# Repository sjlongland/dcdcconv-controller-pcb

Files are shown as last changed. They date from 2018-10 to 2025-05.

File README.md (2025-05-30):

[Find this project on codeberg](https://codeberg.org/sjlongland/dcdcconv-controller-pcb)

As a result of Github's decision to force AI-generated issues with no opt-out,
I am migrating personal projects of mine to Codeberg.  The project at Github
will be archived.

----

# DC-DC Converter Controller

This PCB (using KiCAD 5.0) implements the controller for a DC-DC converter.
It provides differential I²C for connection to a [voltage/current sensor
board](https://codeberg.org/sjlongland/dcdcconv-sensor-pcb) and LVDS outputs for
connection to a [driver
board](https://codeberg.org/sjlongland/dcdcconv-driver-pcb).

The brains of the operation is the Atmel ATTiny861 microcontroller, which
features a high-speed PLL for fast PWM outputs.  The
[firmware](https://codeberg.org/sjlongland/dcdcconv-firmware) polls up to two
sensor boards to make decisions on the PWM duty cycle used to control the
MOSFET driver board.  In theory, the firmware can be expanded to support other
sensor boards and the MOSFET driver board replaced to support other switch
types such as IGBTs for higher power converters.  Use of differential
signalling minimises interference on long cable runs.

The ATTiny861 communicates with a host controller via SPI, allowing it to
communicate with a wide array of host controllers.  This allows for higher-end
host MCUs and application processors that perhaps aren't as good on the PWM
front, to receive notification of when voltage or current levels change
outside given bounds, and thus provide advice on how to adjust the PWM level
to meet requirements.

The host controller can provide the UI functions and higher-level algorithms
such as [MPPT](https://en.wikipedia.org/wiki/Maximum_power_point_tracking)
allowing the ATTiny861 to actually look after the PWM and low-level control.

## Parts list

### To omit:

* U2: Do not fit: for switch controller below only
* C2: Do not fit: localised decoupling for U2.
* J2: Do not fit: GPIO outputs for U2.

### To fit:

* U1: Atmel ATTiny861A-SU
* U3: 74AHC244 tri-state buffer
* U4: NXP PCA9615 Differential I²C controller
* U5: TI SN65LVDS047D 4-channel LVDS driver
* C5: ≥100µF ≥10V 6.3mm SMD electrolytic capacitor (bulk power rail decoupling)
* C1, C3, C4, C6: 100nF ≥10V 0805 ceramic capacitor (localised power rail
  decoupling)
* (**FIT ONE ONLY**) C7, C8, C9, C10: ~100pF ≥20V ceramic capacitor 0805 (0V
  AC de-coupling to chassis.  Choose the one that best suits your mounting
  requirements.)
* R1, R2: 2k2 ohm resistors, 0805 size (I²C pull-ups)
* R3, R4, R5, R6, R7: (approx) 10k ohm resistors, 0805 size (GPIO pull-ups)
* R8, R10: (**NOT CONFIRMED**) 2k2 ohm resistors, 0805 size (differential I²C
  pull-ups)
* R12, R15: (**NOT CONFIRMED**) 2k2 ohm resistors, 0805 size (differential I²C
  pull-downs)
* R9, R11, R12, R14: Spaces for additional pull-up/down resistors on
  differential I²C.  Do not fit unless found to be required.
* R16, R17: (**NOT CONFIRMED**) 100 ohm 0805 (differential I²C termination)
* R22, R26, R30, R34, R24, R28, R32, R36: Spaces for pull-up resistors on
  LVDS.  Do not fit unless found to be required.
* R23, R27, R31, R35, R25, R29, R33, R37: Spaces for pull-down resistors on
  LVDS.  Do not fit unless found to be required.
* R18, R19, R20, R21: Spaces for termination resistors on LVDS.  Do not fit
  unless found to be required.
* J1: 2×7 right-angle 2.54mm header connector (host SPI interface)
* J3, J4: 6-pin 2.54mm "KK" connector (Differential I²C to sensor boards,
  two provided for wiring convenience wired in parallel, use both or
  either.)
* J5: 6-pin 2.54mm "KK" connector (LVDS PWM outputs for buck converter
  MOSFETs)
* J6: 6-pin 2.54mm "KK" connector (LVDS PWM outputs for boost converter
  MOSFETs)

# Switch controller

The board also supports an alternate MCU, the Atmel ATTiny24A, which can be
used in place of the ATTiny861 for simple switch control.  In this
configuration, the LVDS output is dispensed with in favour of a pair of
low-speed GPIOs (one PWMable) which can drive a small signal transistor for
MOSFET control or directly drive solid-state relays.

This latter design is intended for applications such as
[VSRs](https://en.wikipedia.org/wiki/Voltage-sensitive_relay) and power
distribution control using an interface compatible with the full controller.
The controller still supports talking to multiple sensor boards for power
measurement.

## Parts list

### To omit:
* C1, C4, C6: Do not fit: localised decoupling for U1, U3, U5.
* U1, U3, U5: Do not fit: for PWM DC-DC controller above.
* R22, R26, R30, R34, R24, R28, R32, R36, R23, R27, R31, R35, R25, R29, R33,
  R37, R18, R19, R20, R21: Do not fit: pull resistors for LVDS (not used)
* J5, J6: Do not fit: LVDS outputs for PWM controller

### To fit:
* U2: Atmel ATTiny24A-SSU
* U4: NXP PCA9615 Differential I²C controller
* C5: ≥100µF ≥10V 6.3mm SMD electrolytic capacitor (bulk power rail decoupling)
* C2, C3: 100nF ≥10V 0805 ceramic capacitor (localised power rail
  decoupling)
* (**FIT ONE ONLY**) C7, C8, C9, C10: ~100pF ≥20V ceramic capacitor 0805 (0V
  AC de-coupling to chassis.  Choose the one that best suits your mounting
  requirements.)
* R1, R2: 2k2 ohm resistors, 0805 size (I²C pull-ups)
* R3, R4, R5, R6, R7: (approx) 10k ohm resistors, 0805 size (GPIO pull-ups)
* R8, R10: (**NOT CONFIRMED**) 2k2 ohm resistors, 0805 size (differential I²C
  pull-ups)
* R12, R15: (**NOT CONFIRMED**) 2k2 ohm resistors, 0805 size (differential I²C
  pull-downs)
* R9, R11, R12, R14: Spaces for additional pull-up/down resistors on
  differential I²C.  Do not fit unless found to be required.
* R16, R17: (**NOT CONFIRMED**) 100 ohm 0805 (differential I²C termination)
* J1: 2×7 right-angle 2.54mm header connector (host SPI interface)
* J2: 4-pin 2.54mm "KK" connector (GPIO outputs for MOSFET/SSR switch control)
* J3, J4: 6-pin 2.54mm "KK" connector (Differential I²C to sensor boards,
  two provided for wiring convenience wired in parallel, use both or
  either.)

# Host interface

The host interface is via the 14-pin connector at the bottom of the board.
This connector features the following signals:

* Even pins: 0V reference voltage
* Pin 1: 5V power rail
* Pin 3: SPI interface `MOSI` data input
* Pin 5: SPI interface `MISO` data output
* Pin 7: SPI interface `SCK` serial clock
* Pin 9: SPI interface `nCS` Chip select
* Pin 11: SPI interface `nINT` Host interrupt
* Pin 13: `nRESET` Device reset and AVR ICSP.
* Pin 15: `GPIO1` Arbitrary GPIO for application use
* Pin 17: `GPIO0` Arbitrary GPIO for application use

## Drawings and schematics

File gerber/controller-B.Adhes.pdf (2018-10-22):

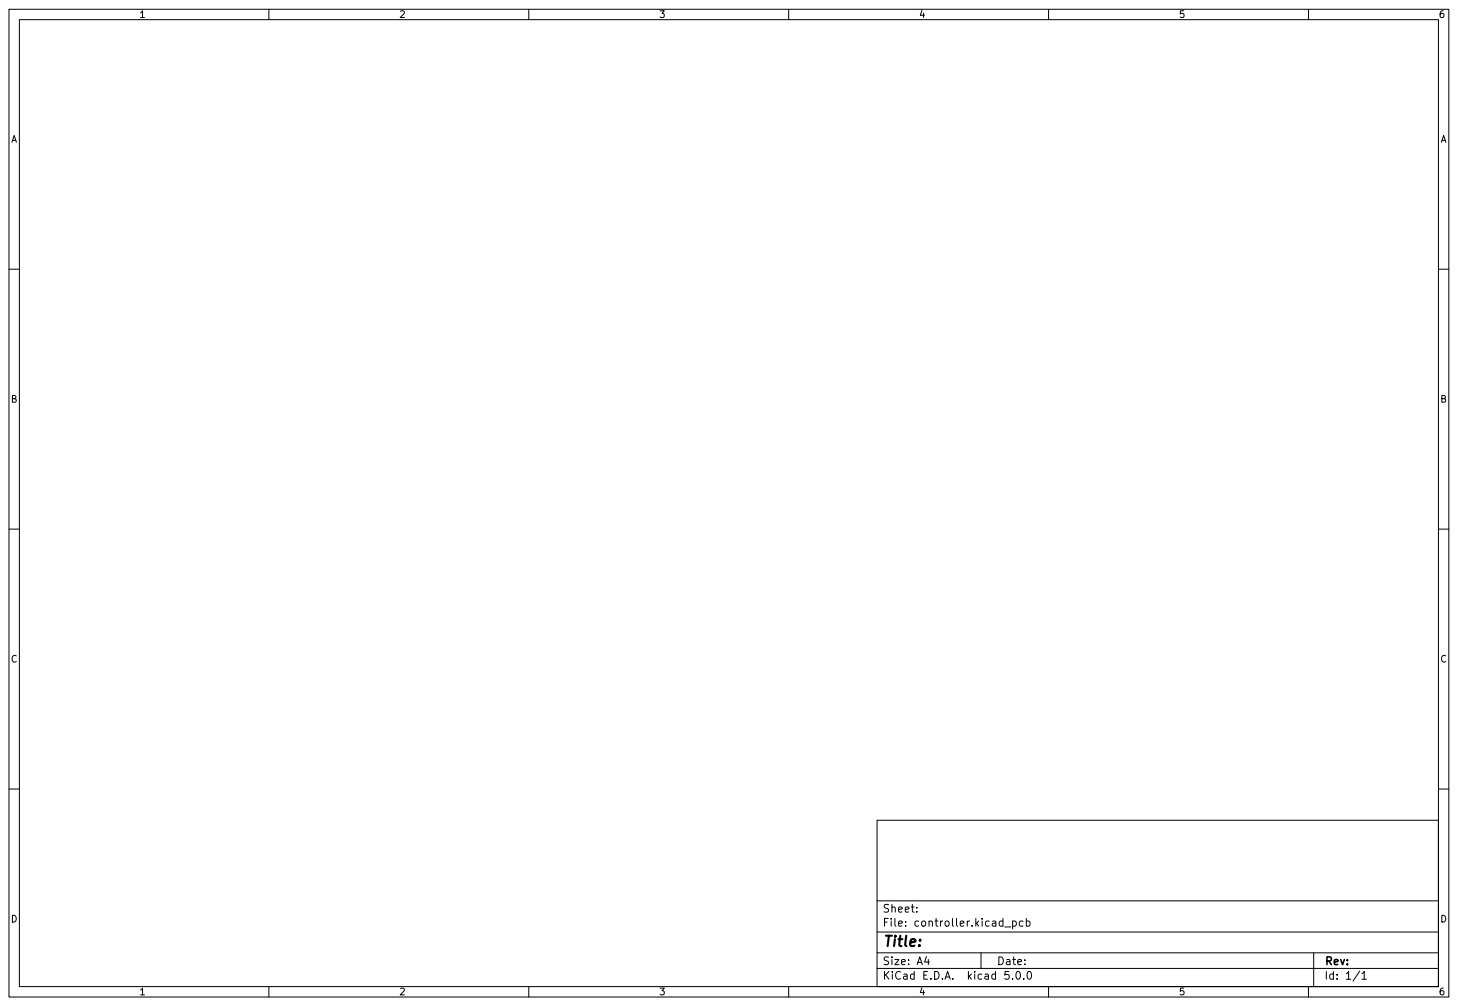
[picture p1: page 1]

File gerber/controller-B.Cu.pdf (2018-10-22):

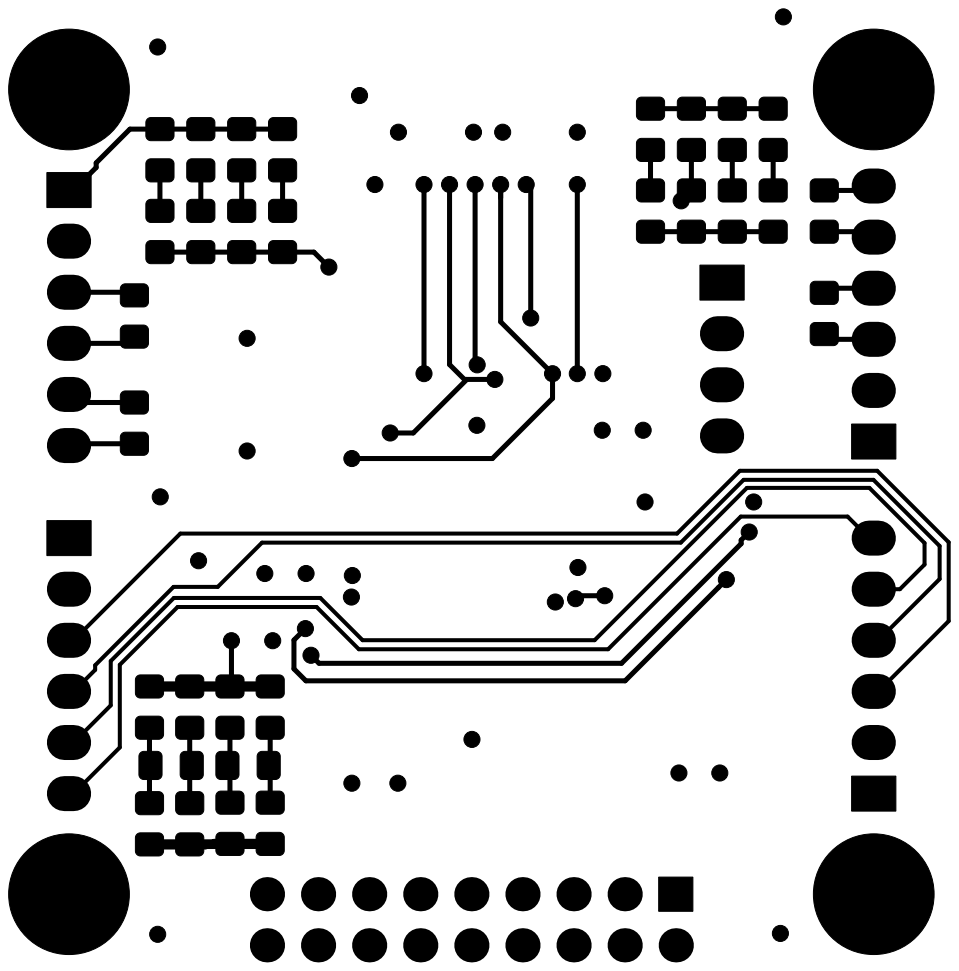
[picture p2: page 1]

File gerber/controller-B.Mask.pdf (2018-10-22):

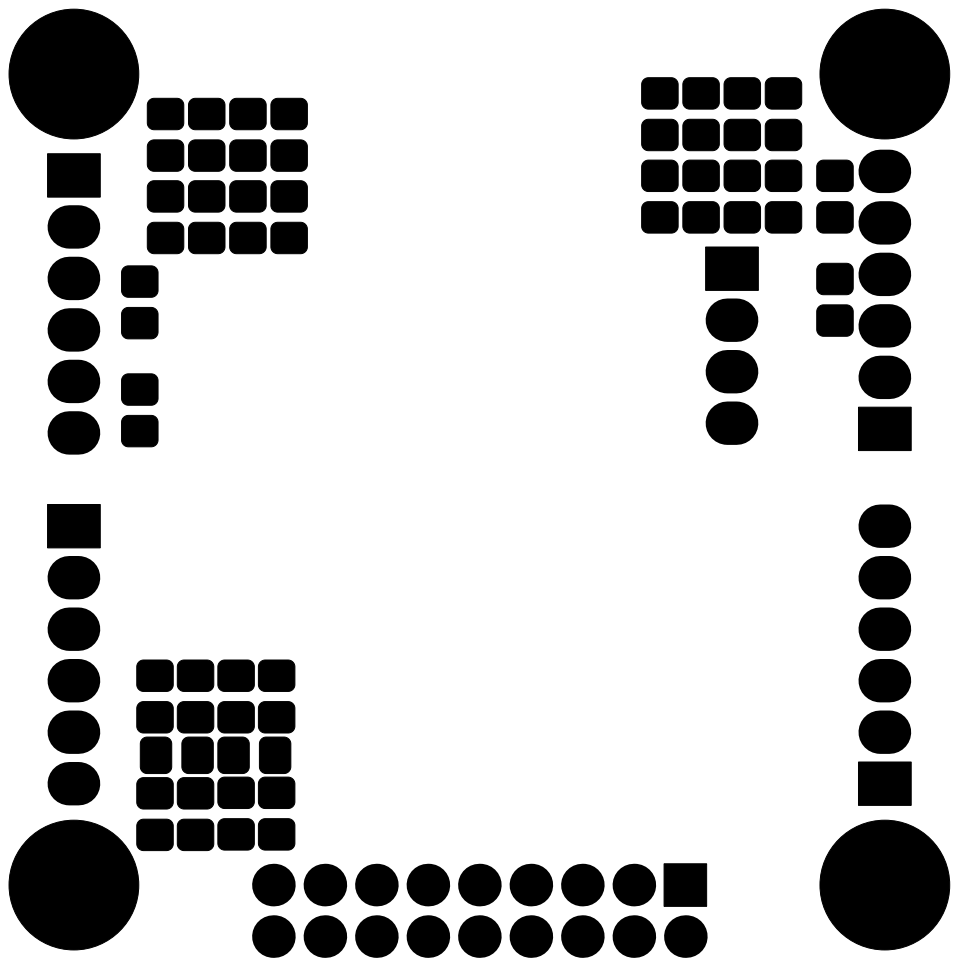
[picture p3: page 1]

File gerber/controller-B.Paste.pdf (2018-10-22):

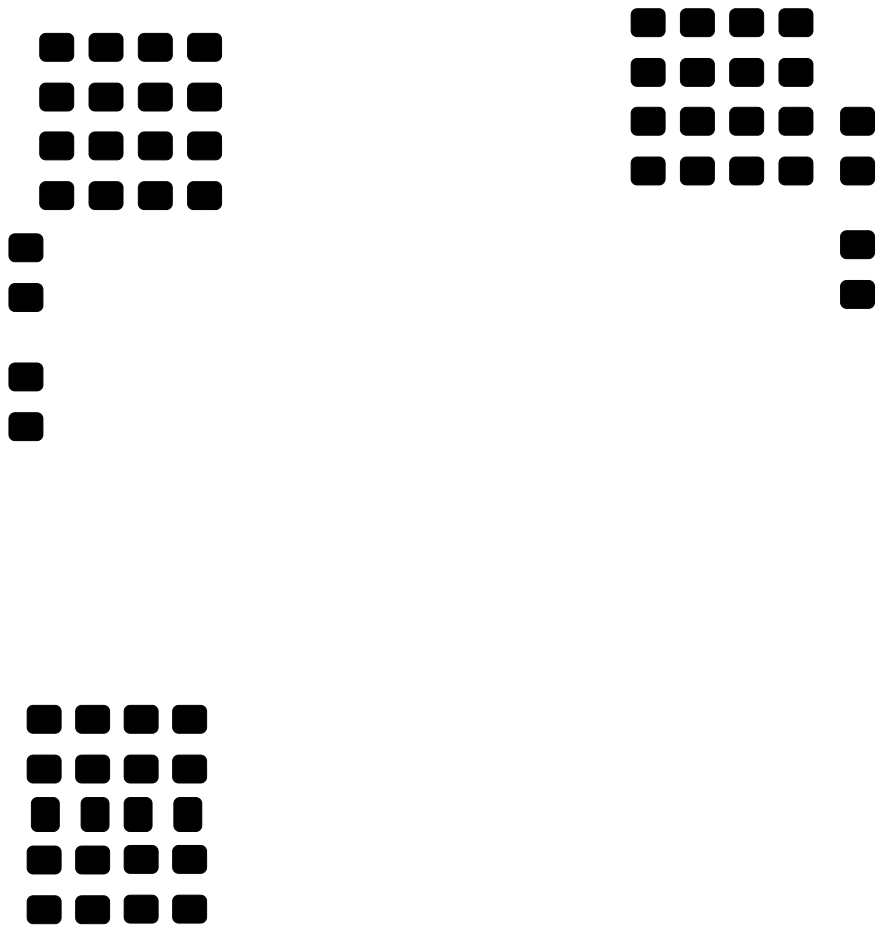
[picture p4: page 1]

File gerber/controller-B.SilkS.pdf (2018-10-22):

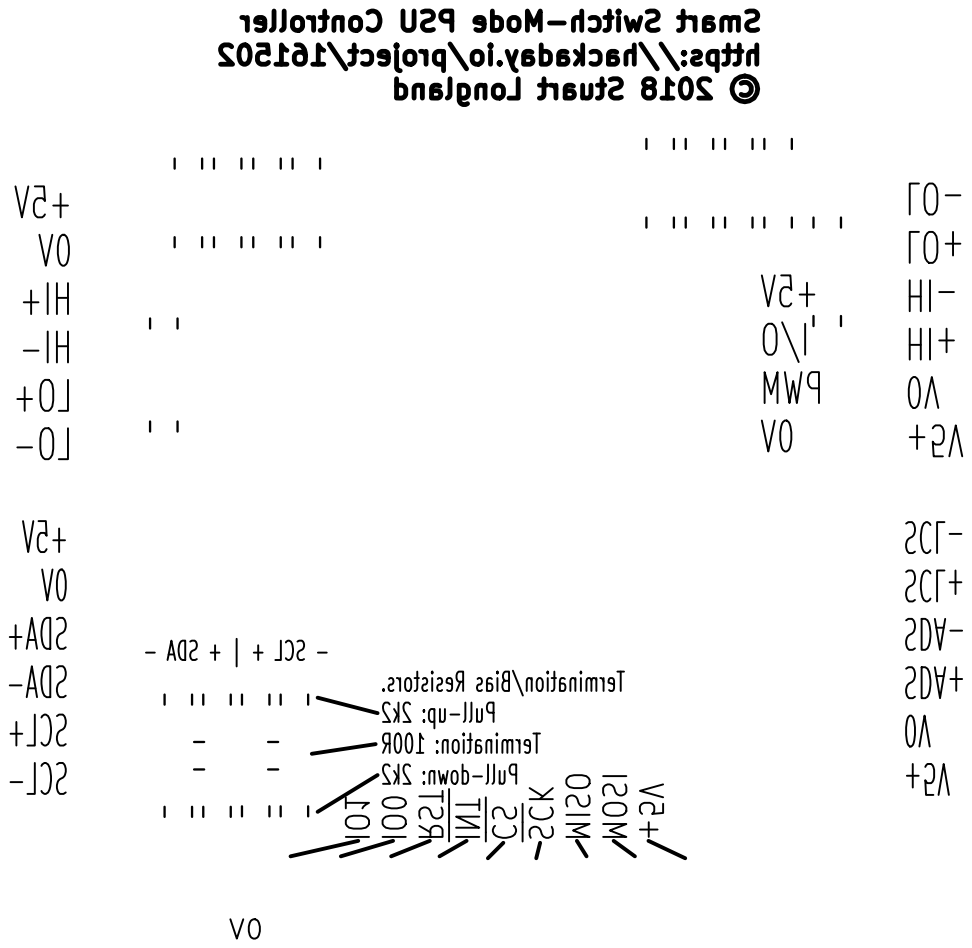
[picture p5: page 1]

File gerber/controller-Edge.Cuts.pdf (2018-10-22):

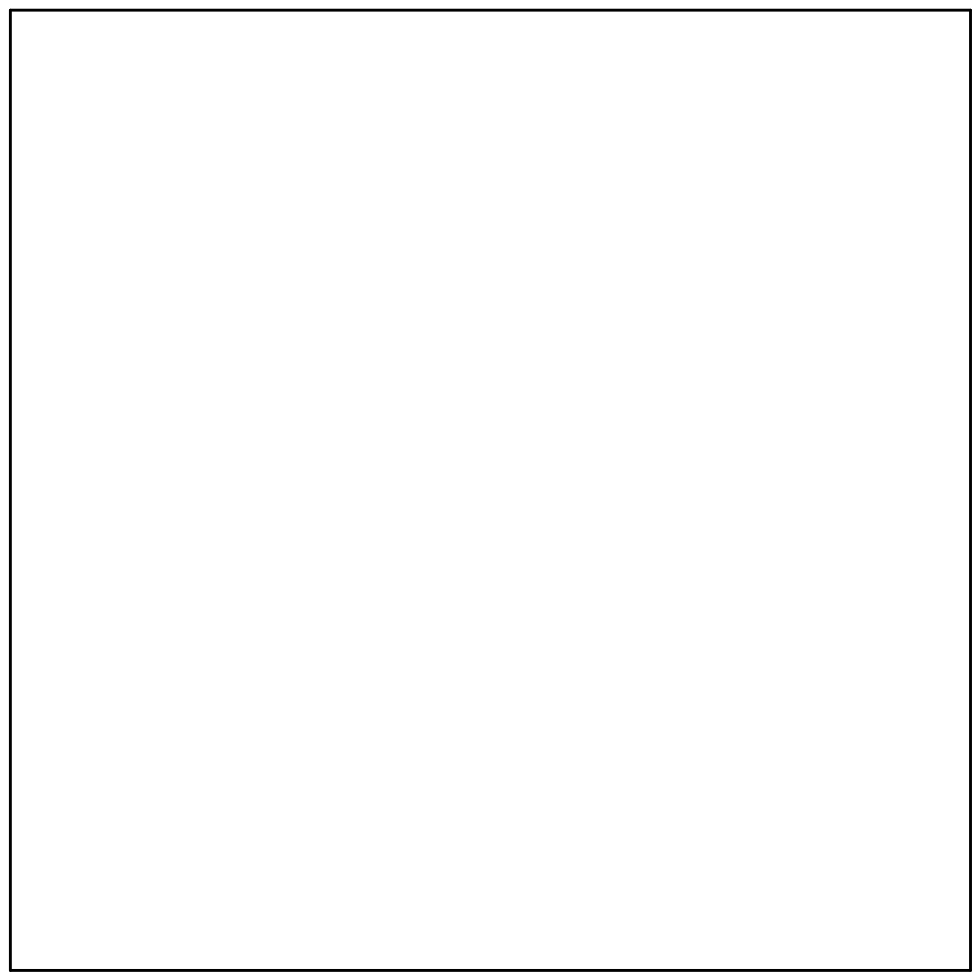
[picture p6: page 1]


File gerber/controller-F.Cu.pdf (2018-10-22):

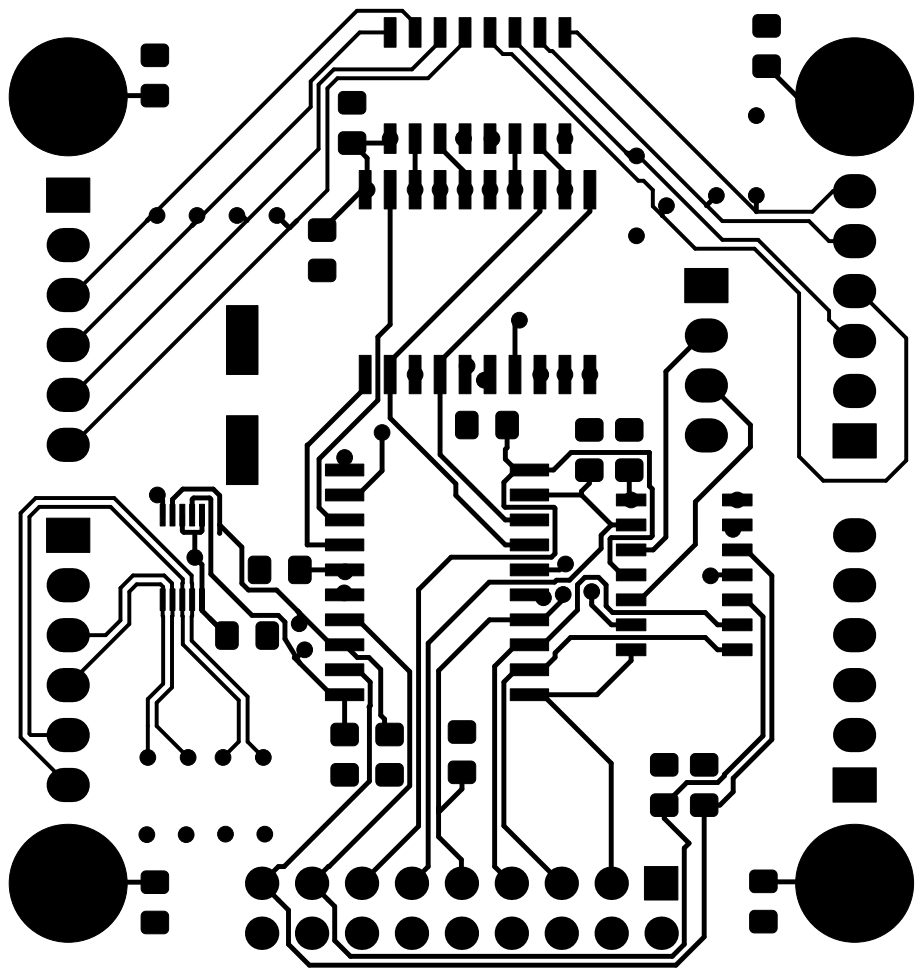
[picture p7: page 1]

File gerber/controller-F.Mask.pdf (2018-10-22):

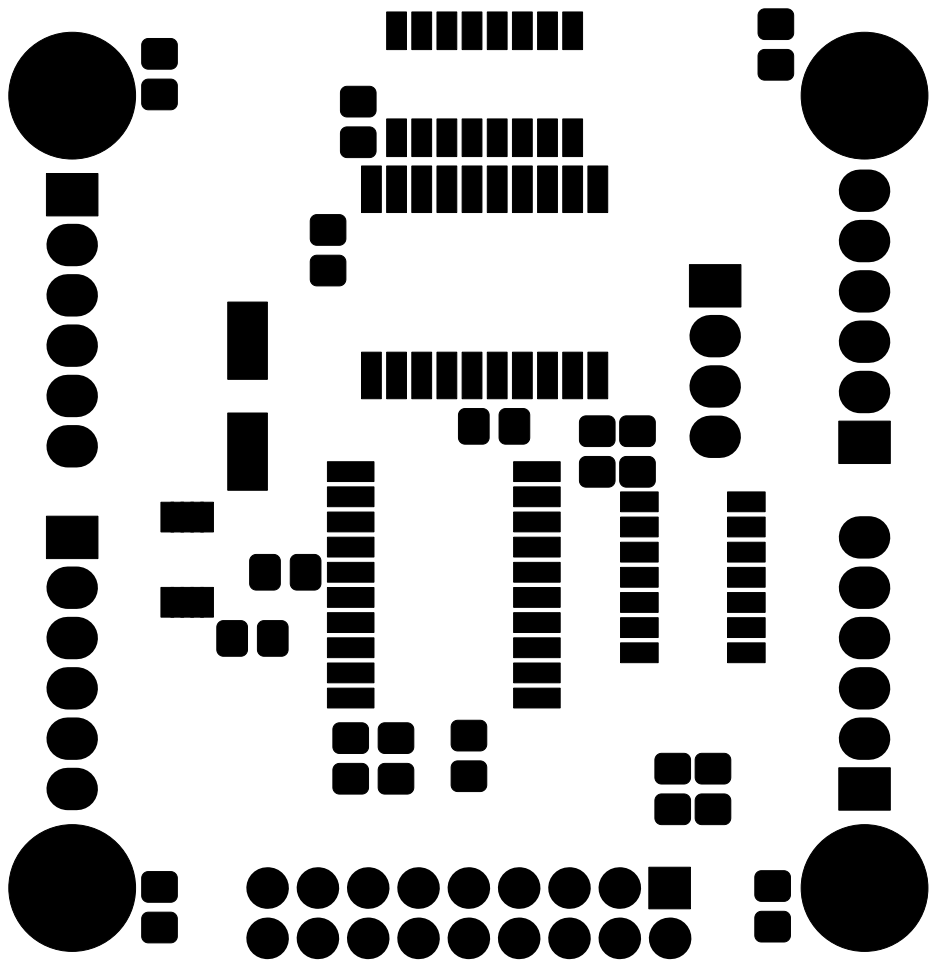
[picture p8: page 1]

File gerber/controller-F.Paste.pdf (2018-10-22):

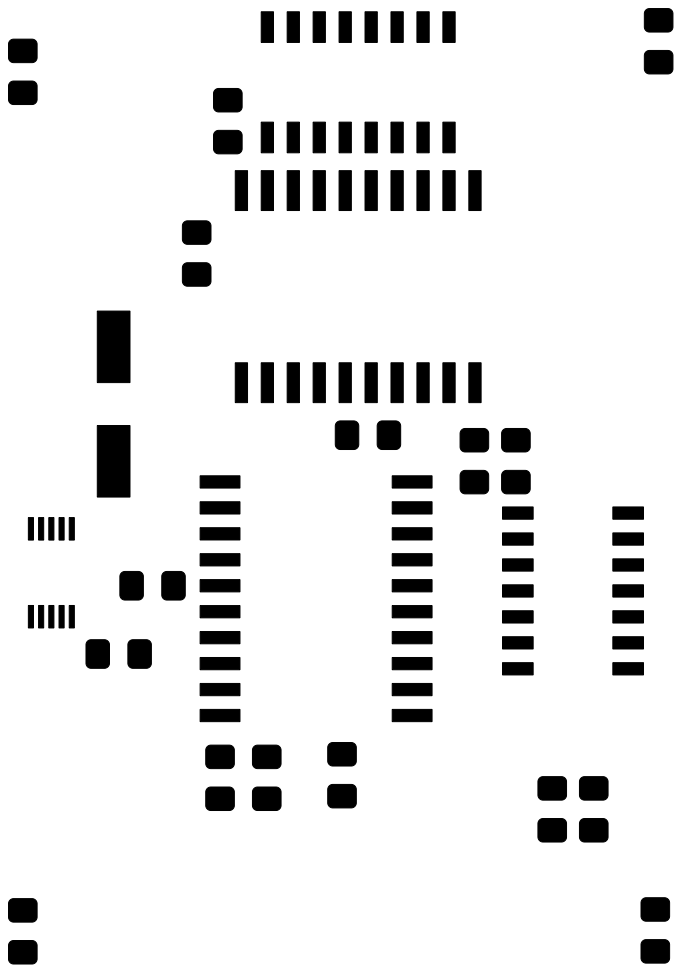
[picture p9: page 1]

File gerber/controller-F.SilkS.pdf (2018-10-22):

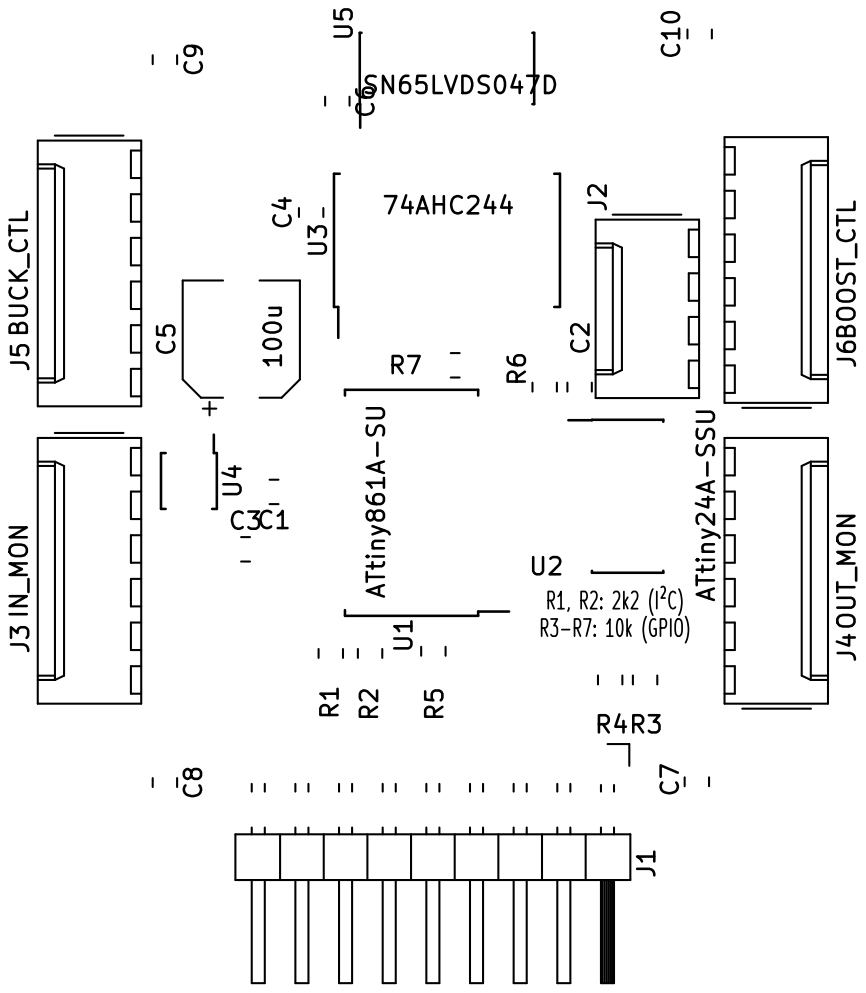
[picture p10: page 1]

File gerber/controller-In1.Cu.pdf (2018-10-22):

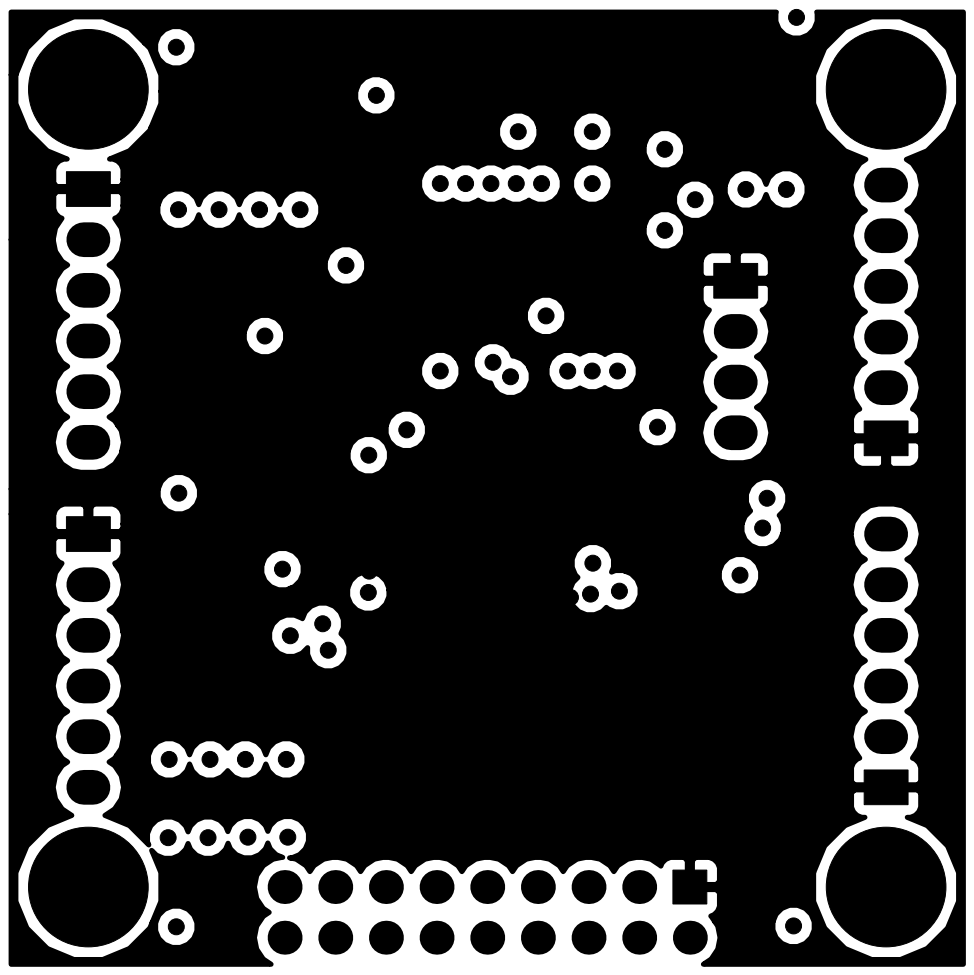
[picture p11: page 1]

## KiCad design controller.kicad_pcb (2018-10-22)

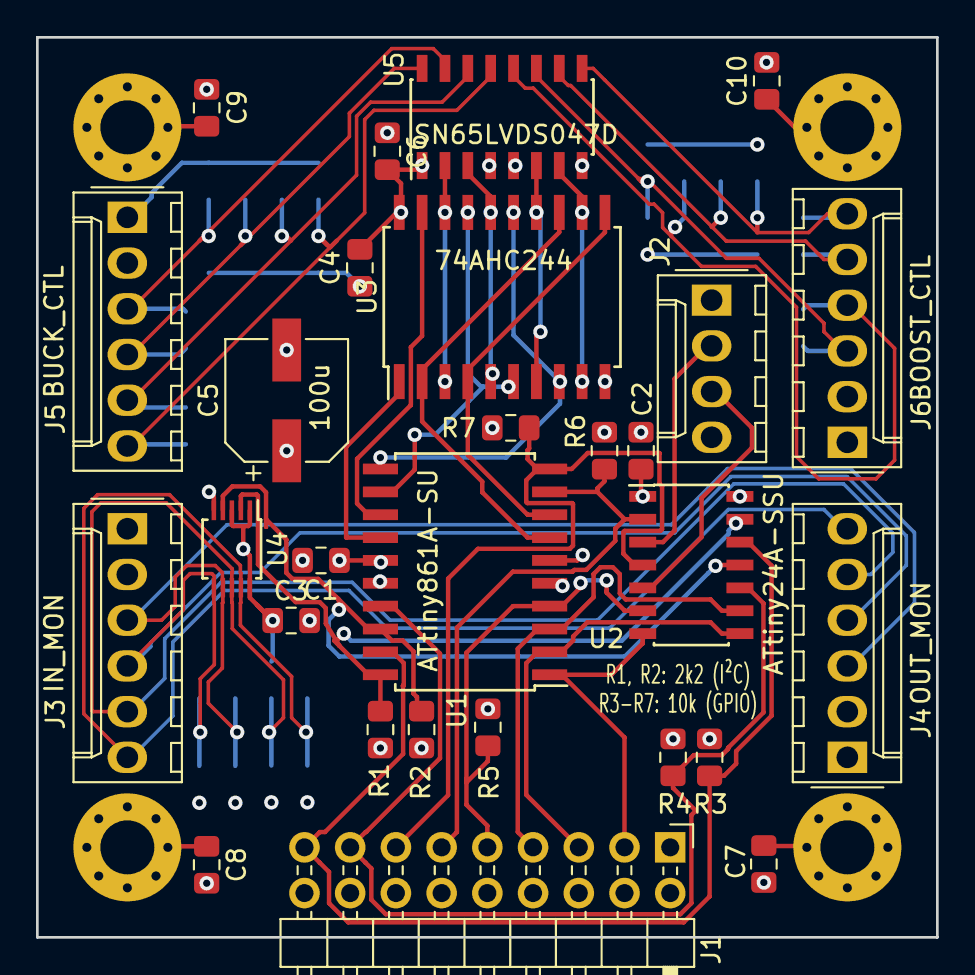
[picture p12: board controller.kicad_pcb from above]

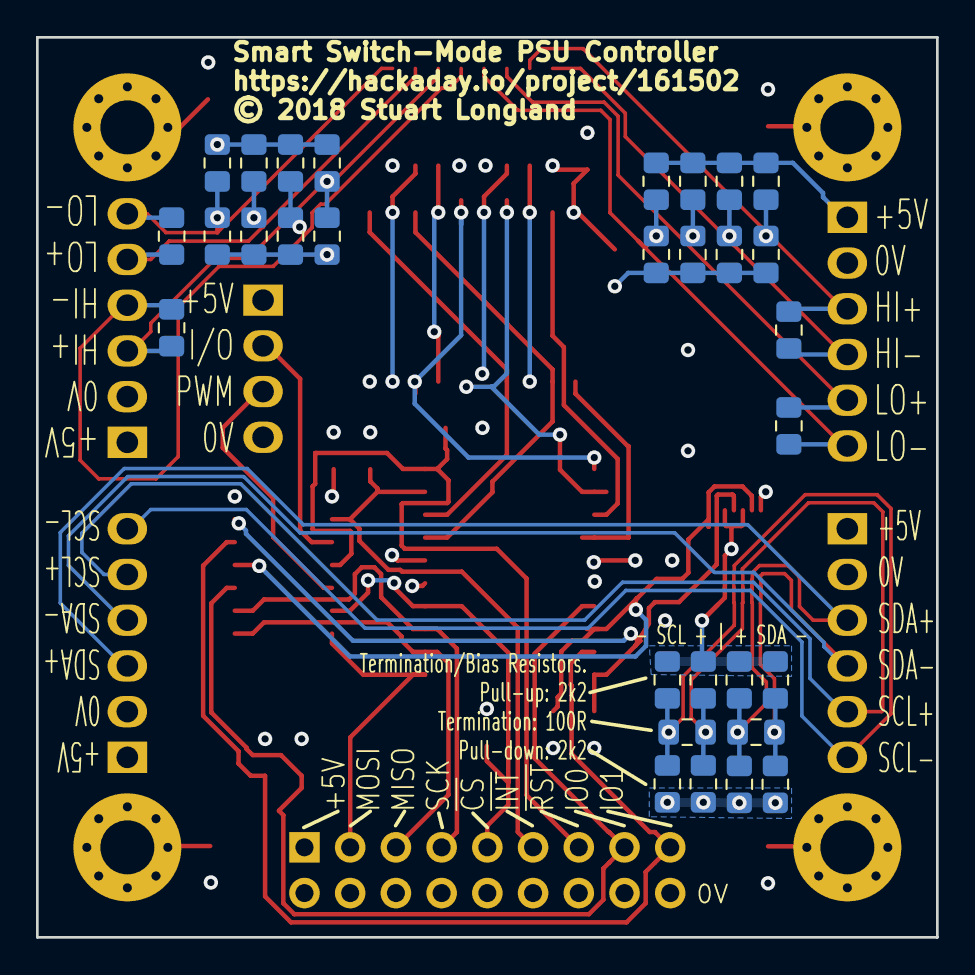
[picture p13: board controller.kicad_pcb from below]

Board: 4 copper layers, 50.0 x 50.0 mm, 62 parts (30 on the bottom side), 40 nets.

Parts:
C1, C2, C3, C4, C6: 100n; C_0805_2012Metric_Pad1.15x1.40mm_HandSolder
C5: 100u; CP_Elec_6.3x9.9
C7, C8, C9, C10: 10p; C_0805_2012Metric_Pad1.15x1.40mm_HandSolder
J1: Conn_02x07_Odd_Even; PinHeader_2x09_P2.54mm_Horizontal
J2: Conn_01x04; Molex_KK-254_AE-6410-04A_1x04_P2.54mm_Vertical
J3: IN_MON; Molex_KK-254_AE-6410-06A_1x06_P2.54mm_Vertical
J4: OUT_MON; Molex_KK-254_AE-6410-06A_1x06_P2.54mm_Vertical
J5: BUCK_CTL; Molex_KK-254_AE-6410-06A_1x06_P2.54mm_Vertical
J6: BOOST_CTL; Molex_KK-254_AE-6410-06A_1x06_P2.54mm_Vertical
MH1, MH2, MH3, MH4: MountingHole_Pad; MountingHole_3mm_Pad_Via
R1, R2, R8, R9, R10, R11, R12, R13, R14, R15, R22, R23, R24, R25, R26, R27, R28, R29, R30, R31, R32, R33, R34, R35, R36, R37: 2k2; R_0805_2012Metric_Pad1.15x1.40mm_HandSolder
R3, R4, R5, R6, R7: 10k; R_0805_2012Metric_Pad1.15x1.40mm_HandSolder
R16, R17, R18, R19, R20, R21: 100R; R_0805_2012Metric_Pad1.15x1.40mm_HandSolder
U1: ATtiny861A-SU; SOIC-20W_7.5x12.8mm_P1.27mm
U2: ATtiny24A-SSU; SOIC-14_3.9x8.7mm_P1.27mm
U3: 74AHC244; SOIC-20W_7.5x12.8mm_P1.27mm
U4: PCA9615; TSSOP-10_3x3mm_P0.5mm
U5: SN65LVDS047D; SOIC-16_3.9x9.9mm_P1.27mm

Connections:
/BOOST_HI: U3.7, U3.14, U5.6
/BOOST_HI+: J6.3, R20.2, R24.2, R25.1, U5.11
/BOOST_HI-: J6.4, R20.1, R28.2, R29.1, U5.12
/BOOST_LO: U3.9, U3.12, U5.7
/BOOST_LO+: J6.5, R21.2, R32.2, R33.1, U5.10
/BOOST_LO-: J6.6, R21.1, R36.2, R37.1, U5.9
/BUCK_HI: U3.3, U3.18, U5.2
/BUCK_HI+: J5.3, R18.2, R22.2, R23.1, U5.15
/BUCK_HI-: J5.4, R18.1, R26.2, R27.1, U5.16
/BUCK_LO: U3.5, U3.16, U5.3
/BUCK_LO+: J5.5, R19.1, R30.2, R31.1, U5.14
/BUCK_LO-: J5.6, R19.2, R34.2, R35.1, U5.13
/GPIO0: J1.17, R3.2, U1.19, U2.12
/GPIO1: J1.15, R4.2, U1.17, U2.10
/HI_DRV: U1.12, U3.6, U3.17
/LO_DRV: U1.11, U3.8, U3.15
/MISO: J1.5, U1.2, U2.8
/MOSI: J1.3, U1.1, U2.7
/PWM: U1.8, U3.4, U3.11
/SCK: J1.7, U1.3, U2.9
/SCL: R2.2, U1.18, U2.11, U4.4
/SCL+: J3.5, J4.5, R10.2, R14.1, R17.2, U4.8
/SCL-: J3.6, J4.6, R11.2, R15.1, R17.1, U4.9
/SDA: R1.2, U1.20, U2.13, U4.2
/SDA+: J3.3, J4.3, R8.2, R12.1, R16.1, U4.7
/SDA-: J3.4, J4.4, R9.2, R13.1, R16.2, U4.6
/T24_IO: J2.2, U2.3
/T24_PWM: J2.3, U2.5
/~BOOST_PWM_EN~: U1.13, U3.19
/~BUCK_PWM_EN~: U1.14, U3.1
/~CS~: J1.9, R5.2, U1.4, U2.6
/~INT~: J1.11, R6.2, U1.9, U2.2
/~PWM~: U1.7, U3.2, U3.13
/~RESET~: J1.13, R7.2, U1.10, U2.4
GND: C1.2, C2.2, C3.2, C4.1, C5.2, C6.1, C7.2, C8.2, C9.2, C10.2, J1.2, J1.4, J1.6, J1.8, J1.10, J1.12, J1.14, J1.16, J1.18, J2.4, J3.2, J4.2, J5.2, J6.2, R12.2, R13.2, R14.2, R15.2, R23.2, R25.2, R27.2, R29.2, R31.2, R33.2, R35.2, R37.2, U1.6, U1.16, U2.14, U3.10, U4.5, U5.5, U5.8
unnamed: C7.1, MH1.1
unnamed: C8.1, MH2.1
unnamed: C9.1, MH3.1
unnamed: C10.1, MH4.1
VCC: C1.1, C2.1, C3.1, C4.2, C5.1, C6.2, J1.1, J2.1, J3.1, J4.1, J5.1, J6.1, R1.1, R2.1, R3.1, R4.1, R5.1, R6.1, R7.1, R8.1, R9.1, R10.1, R11.1, R22.1, R24.1, R26.1, R28.1, R30.1, R32.1, R34.1, R36.1, U1.5, U1.15, U2.1, U3.20, U4.1, U4.3, U4.10, U5.1, U5.4

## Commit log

2018-10-07 Initial check-in
    [controller.kicad_pcb, controller.sch]
2018-10-07 VCC plane: Move in by 1mm.
    This should reduce any possibility of EMI "leaking" from the VCC plane.
    [controller.kicad_pcb]
2018-10-22 PCB: Finalise layout
    [controller.kicad_pcb]
2018-10-22 gerber: Add CAM files for production.
    [controller-B.Cu.gbl, controller-B.Mask.gbs, controller-B.Paste.gbp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]

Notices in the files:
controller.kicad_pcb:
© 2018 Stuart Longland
